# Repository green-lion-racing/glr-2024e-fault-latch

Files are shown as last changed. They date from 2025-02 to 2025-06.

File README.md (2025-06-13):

# Fault latch for IMD and BMS/AMS

This board is a fork of [JacobParent7/FSAE_ELECTRONICS](https://github.com/JacobParent7/FSAE_ELECTRONICS/tree/main/Fault%20Latch). Thanks!

### Overview

It is stripped down for our purposes of using it just as a fault latch if either IMD or BMS signal an error. So it can open and close the SDC (Shutdown circuit).

As input it needs +12V and GND. It also takes a high input of both IMD and BMS to register a fault.

It has two outputs for LEDs, these go into the cockpit of the car, to signal issues to the driver.

Lastly there is one connection where the SDC is routed through.

### Used parts

> [!WARNING]  
> Part list is not available currently.

| Article | Description | Link | Quantity |
| --- | --- | ---- | --- |
| | | | |
| | | | |
| | | | |
| | | | |
| | | | |

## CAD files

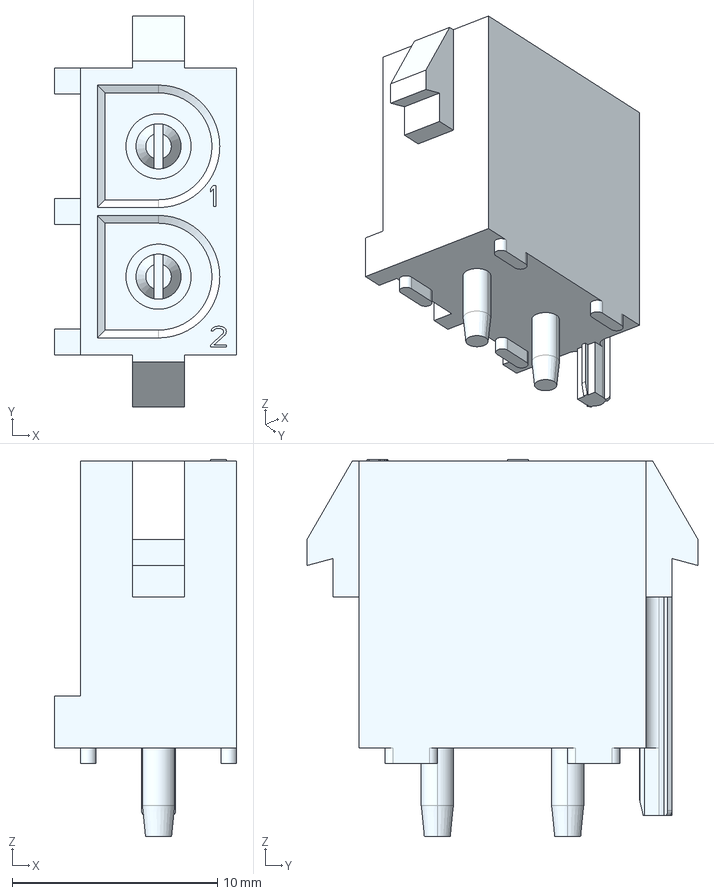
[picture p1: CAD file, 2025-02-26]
DOWNLOADS/CONN/c-641964-1-p-3d.stp
8.89 x 19.1 x 18.4 mm

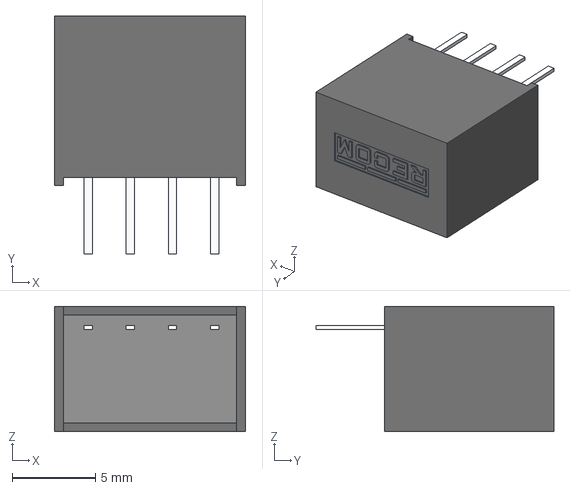
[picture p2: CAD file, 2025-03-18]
DOWNLOADS/ISOLATED_CONVERTER/KiCad/RI-1205S.stp
11.5 x 14.3 x 7.55 mm

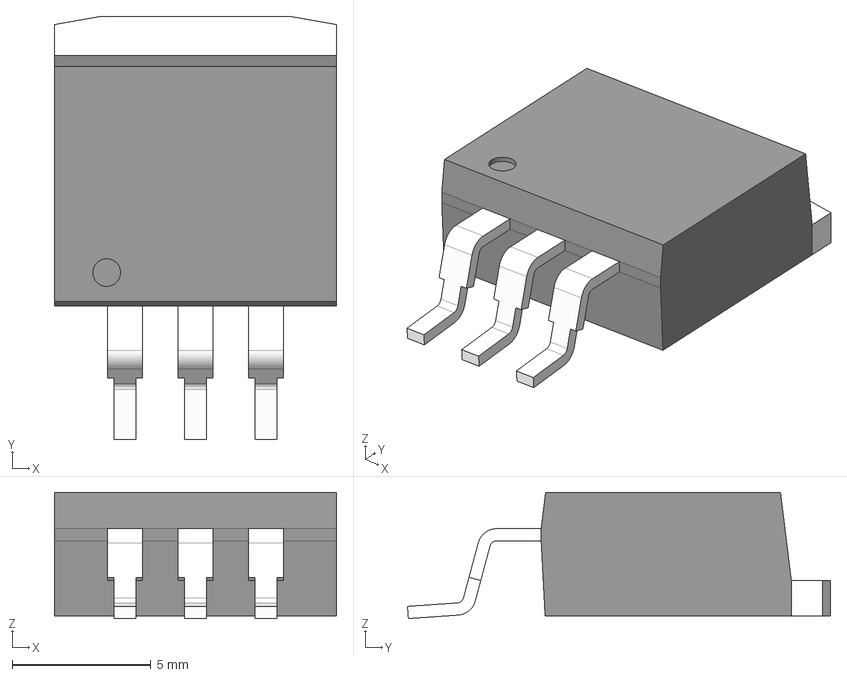
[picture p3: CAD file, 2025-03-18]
DOWNLOADS/REGULATOR/LM7805SX_NOPB.stp
10.2 x 15.2 x 4.54 mm
BODY-TO
HTSINK-TO263
LEAD-TO263 x 3

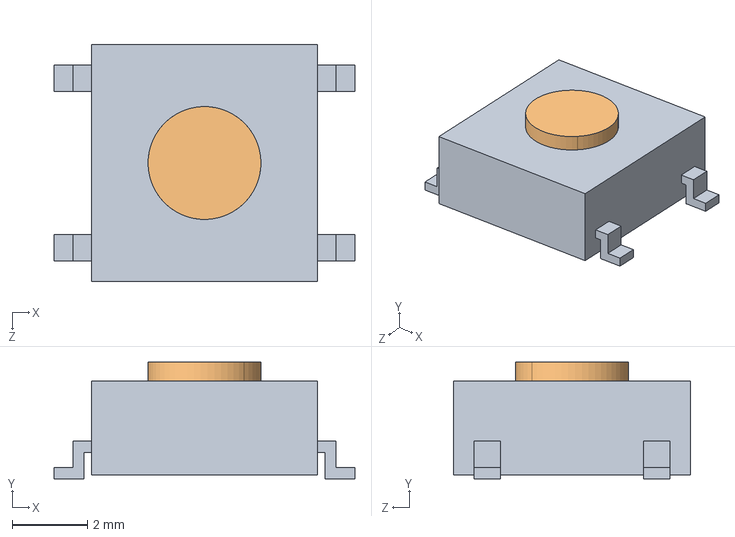
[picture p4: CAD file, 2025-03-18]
DOWNLOADS/SWITCH_3D/B3FS_1000.step
8.00 x 3.10 x 6.30 mm
B3FS_1000_BASE
B3FS_1000_BUTTON

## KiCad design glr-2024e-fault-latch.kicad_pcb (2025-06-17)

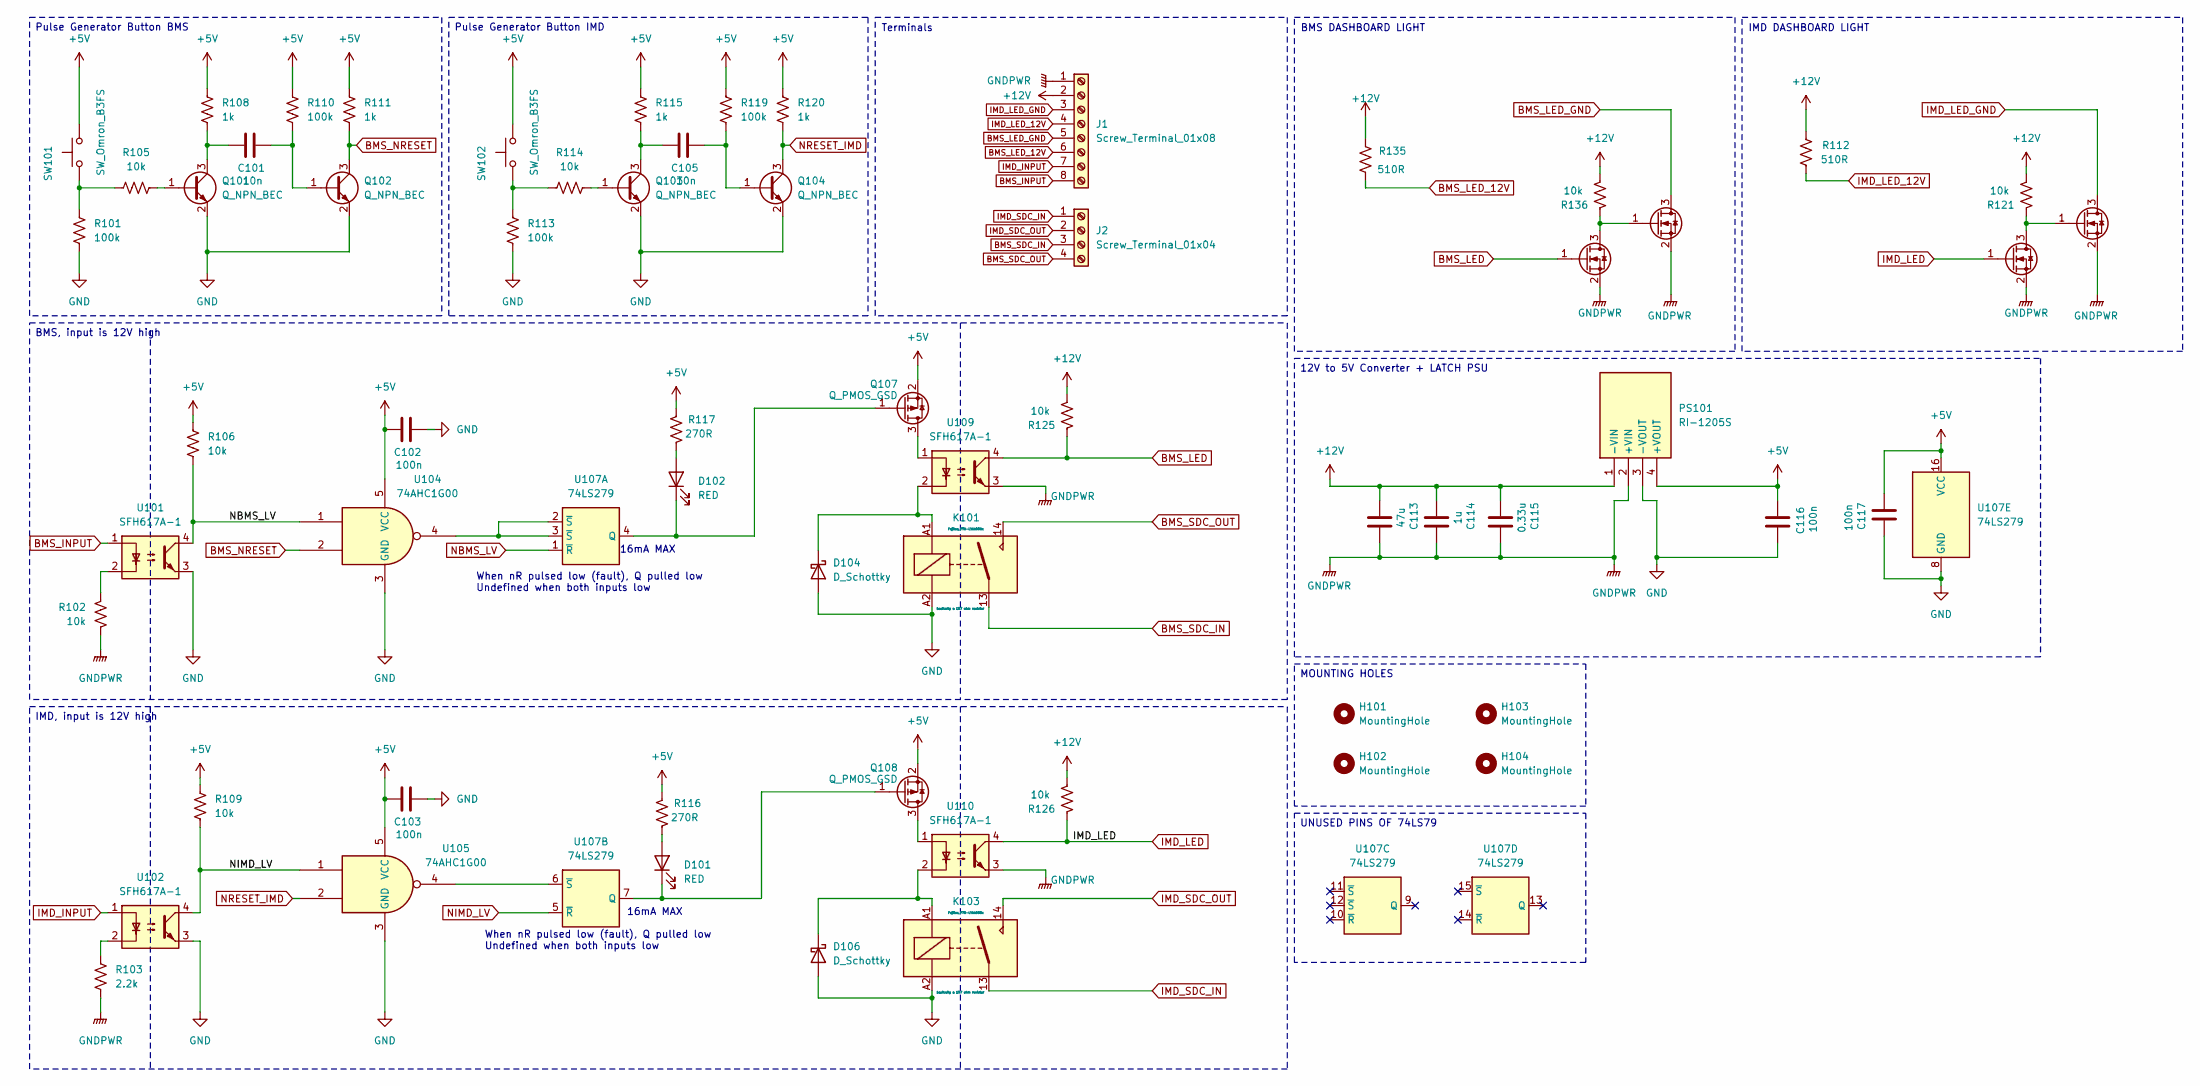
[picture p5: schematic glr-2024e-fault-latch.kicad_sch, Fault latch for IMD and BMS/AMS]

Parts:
C101, C105: 10n; C_0603_1608Metric_Pad1.08x0.95mm_HandSolder; JLC# C1589
C102, C103, C116, C117: 100n; C_0603_1608Metric_Pad1.08x0.95mm_HandSolder; JLC# C1591
C113: 47u; CP_Elec_6.3x5.4; JLC# C2836440
C114: 1u; C_0805_2012Metric_Pad1.18x1.45mm_HandSolder; JLC# C91186
C115: 0.33u; C_0603_1608Metric_Pad1.08x0.95mm_HandSolder; JLC# C282682
D101, D102: RED; LED_0805_2012Metric_Pad1.15x1.40mm_HandSolder; JLC# C19171391
D104, D106: D_Schottky; D_SMA; JLC# C8678
H101, H102, H103, H104: MountingHole; MountingHole_3.2mm_M3
J1: Screw_Terminal_01x08; WECO-950-FB-08
J2: Screw_Terminal_01x04; WECO-950-FB-04
K101, K103: Fujitsu_FTR-LYAA005x; Relay_SPST-NO_Fujitsu_FTR-LYAA005x_FormA_Vertical; MOUSER 817-FTR-LYAA005Y
PS101: RI-1205S; RI0505S; Mouser Part Number 919-RI-1205S
Q101, Q102, Q103, Q104: Q_NPN_BEC; SOT-23; JLC# C2146
Q105, Q106, Q114, Q115: Q_NMOS_GSD; SOT-23; JLC# C151421
Q107, Q108: Q_PMOS_GSD; SOT-523; JLC# C96676
R101, R110, R113, R119: 100k; R_0805_2012Metric_Pad1.20x1.40mm_HandSolder; JLC# C149504
R102, R106, R109, R121, R125, R126, R136: 10k; R_0805_2012Metric_Pad1.20x1.40mm_HandSolder; MOUSER ESR10EZPD1002
R103: 2.2k; R_0805_2012Metric_Pad1.20x1.40mm_HandSolder; JLC# C17520
R105, R114: 10k; R_0805_2012Metric_Pad1.20x1.40mm_HandSolder; JLC# C17414
R108, R111, R115, R120: 1k; R_0805_2012Metric_Pad1.20x1.40mm_HandSolder; JLC# C17513
R112, R135: 510R; R_0603_1608Metric; MOUSER KTR03EZPF5100
R116, R117: 270R; R_0805_2012Metric_Pad1.20x1.40mm_HandSolder; JLC# C17590
SW101, SW102: SW_Omron_B3FS; SW_SPST_Omron_B3FS-100xP; JLC# C271750
U101, U102, U109, U110: SFH617A-1; DIP-4_W7.62mm; MOUSER SFH617A-1X007T
U104, U105: 74AHC1G00; SOT-23-5; JLC# C350556
U107: 74LS279; SOIC-16_3.9x9.9mm_P1.27mm; MOUSER 595-SN74LS279ADR

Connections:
+5V: C102.1, C103.1, C116.2, C117.1, PS101.4 (+VOUT), Q107.2 (S), Q108.2 (S), R106.1, R108.1, R109.1, R110.1, R111.1, R115.1, R116.2, R117.2, R119.1, R120.1, SW101.2, SW102.2, U104.5 (VCC), U105.5 (VCC), U107.16 (VCC)
+12V: C113.2, C114.2, C115.2, J1.2, PS101.1 (-VIN), R112.1, R121.1, R125.1, R126.1, R135.1, R136.1
BMS_INPUT: J1.8, U101.1
BMS_LED: Q114.1 (G), R125.2, U109.4
BMS_LED_12V: J1.6, R135.2
BMS_LED_GND: J1.5, Q115.3 (D)
BMS_NRESET: Q102.3 (C), R111.2, U104.2
BMS_SDC_IN: J2.3, K101.13
BMS_SDC_OUT: J2.4, K101.14
GND: C102.2, C103.2, C116.1, C117.2, D104.2 (A), D106.2 (A), K101.A2, K103.A2, PS101.3 (-VOUT), Q101.2 (E), Q102.2 (E), Q103.2 (E), Q104.2 (E), R101.2, R113.2, U101.3, U102.3, U104.3 (GND), U105.3 (GND), U107.8 (GND)
GNDPWR: C113.1, C114.1, C115.1, J1.1, PS101.2 (+VIN), Q105.2 (S), Q106.2 (S), Q114.2 (S), Q115.2 (S), R102.1, R103.2, U109.3, U110.3
IMD_INPUT: J1.7, U102.1
IMD_LED: Q105.1 (G), R126.2, U110.4
IMD_LED_12V: J1.4, R112.2
IMD_LED_GND: J1.3, Q106.3 (D)
IMD_SDC_IN: J2.1, K103.13
IMD_SDC_OUT: J2.2, K103.14
NBMS_LV: R106.2, U101.4, U104.1, U107.1 (~R)
NIMD_LV: R109.2, U102.4, U105.1, U107.5 (~R)
NRESET_IMD: Q104.3 (C), R120.2, U105.2
unnamed: D101.2 (A), R116.1
unnamed: D101.1 (K), Q108.1 (G), U107.7 (Q)
unnamed: D102.2 (A), R117.1
unnamed: D102.1 (K), Q107.1 (G), U107.4 (Q)
unnamed: D104.1 (K), K101.A1, U109.2
unnamed: D106.1 (K), K103.A1, U110.2
unnamed: Q101.1 (B), R105.1
unnamed: C101.1, Q101.3 (C), R108.2
unnamed: C101.2, Q102.1 (B), R110.2
unnamed: Q103.1 (B), R114.1
unnamed: C105.1, Q103.3 (C), R115.2
unnamed: C105.2, Q104.1 (B), R119.2
unnamed: Q105.3 (D), Q106.1 (G), R121.2
unnamed: Q107.3 (D), U109.1
unnamed: Q108.3 (D), U110.1
unnamed: Q114.3 (D), Q115.1 (G), R136.2
unnamed: R101.1, R105.2, SW101.1
unnamed: R102.2, U101.2
unnamed: R103.1, U102.2
unnamed: R113.1, R114.2, SW102.1
unnamed: U104.4, U107.2 (~S), U107.3 (~S)
unnamed: U105.4, U107.6 (~S)

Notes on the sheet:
16mA MAX
When nR pulsed low (fault), Q pulled low Undefined when both inputs low
BMS, input is 12V high
Pulse Generator Button BMS
Terminals
UNUSED PINS OF 74LS79
Pulse Generator Button IMD
12V to 5V Converter + LATCH PSU
MOUNTING HOLES
BMS DASHBOARD LIGHT
IMD, input is 12V high
IMD DASHBOARD LIGHT

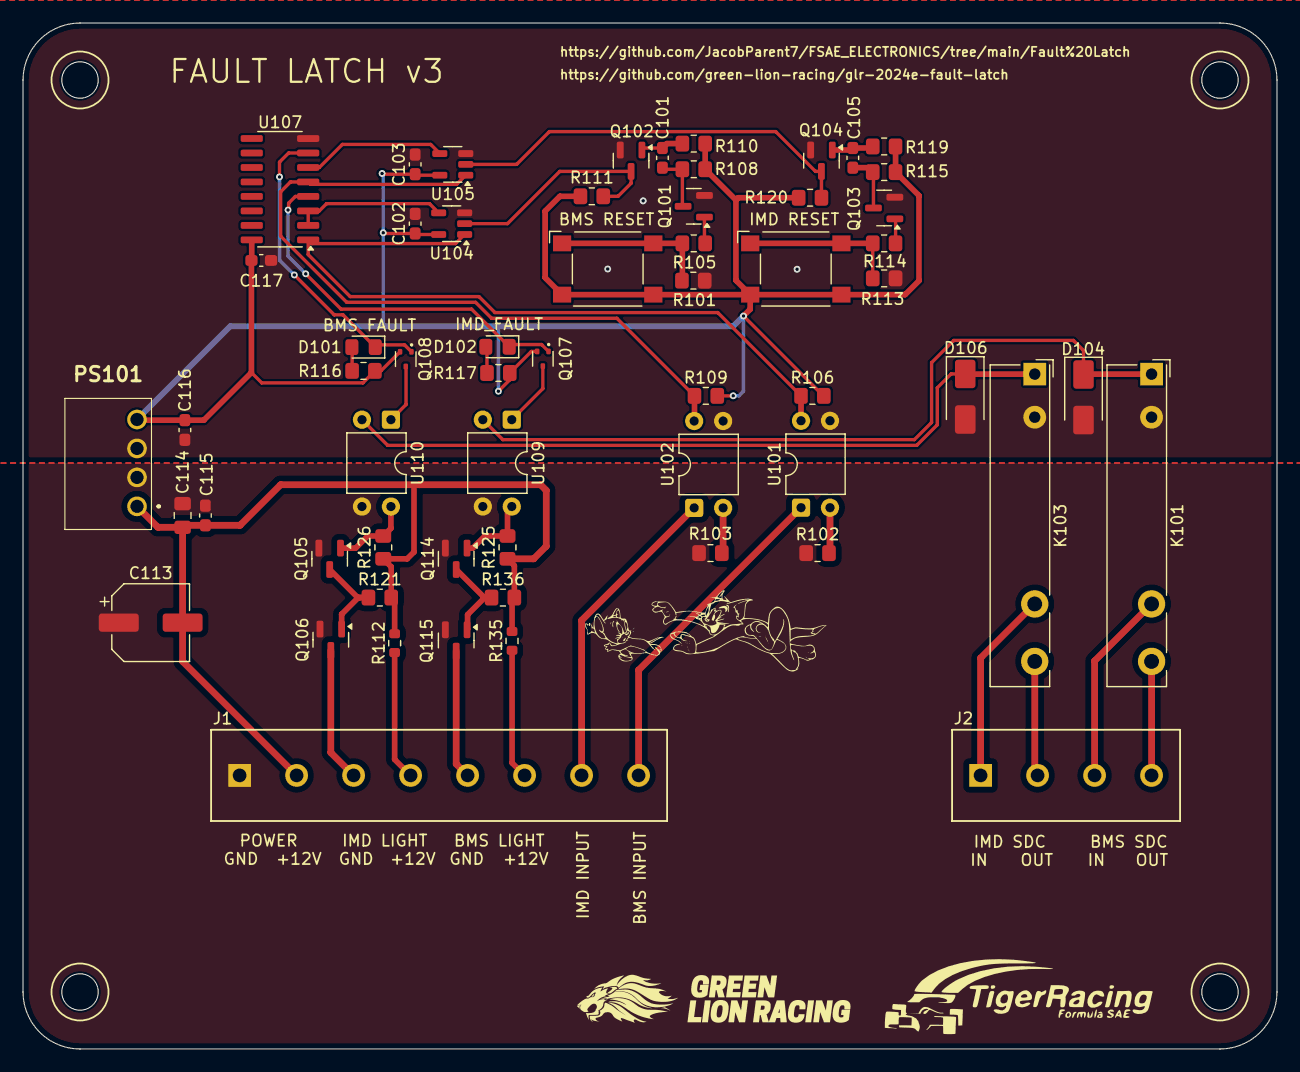
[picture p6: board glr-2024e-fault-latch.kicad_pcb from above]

Board: 2 copper layers, 110.0 x 90.0 mm, 63 parts (0 on the bottom side), 42 nets.

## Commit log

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2025-02-13 Fixed one logical error. Added LT Spice simulation. Pullup Caps, resistor values, schematic layout and cleanup needed.
    [BSPD.kicad_sch]
2025-02-15 Added Current work on Fault Latch
    [Fault Latch 2.kicad_pcb, Fault Latch 2.kicad_sch, Revised Fault Latch Schematic.kicad_pcb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]
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2025-02-19 To Dos on Fault Latch and RML AGAIN.
    [Fault Latch 2.kicad_sch, RML.kicad_pcb, RML.kicad_sch]
2025-02-19 TSSI FIXES
    [TTSI.kicad_sch]
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2025-02-19 TSSI BOM and BYPASS
    [TTSI.kicad_pcb, TTSI.kicad_sch]
2025-02-21 Unfinished version of Fault Latch after applying separate circuits
    [Fault Latch 2.kicad_sch]
2025-02-21 Fault Latch Revision without PSpice Check
    [Fault Latch 2.kicad_sch]
2025-02-21 RML Fixes
    [RML.kicad_sch]
2025-02-21 Comments on BSPD, TSSI
    [BSPD.kicad_sch, TTSI.kicad_sch]
2025-02-22 Added theory of operation to BSPD
    [BSPD.kicad_sch]
2025-02-24 Edits to Fault Latch and TSSI
    [Fault Latch 2.kicad_sch, TTSI.kicad_sch]
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2025-03-02 Added series resistor to RML
    [RML.kicad_sch]
2025-03-02 Added footprints,implemented changes from meeting, starting layout
    [BSPD.kicad_pcb, BSPD.kicad_sch, D0014A.stp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]
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2025-03-08 Fixed the logic for IMD and BSPD
    [Fault Latch 2.kicad_sch]
2025-03-09 Added some footprints but also realized stuff about rules we need to change fault latch for
    [Fault Latch 2.kicad_pcb, Fault Latch 2.kicad_sch]
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2025-03-12 TSSI and FL fixes
    [Fault Latch 2.kicad_sch, TTSI.kicad_pcb, TTSI.kicad_sch]
2025-03-12 Added the pulse generators for the buttons
    [Fault Latch 2.kicad_sch]
2025-03-16 Few changes to BOM as well as added 12v to bunny ears
    [TTSI.kicad_pcb, TTSI.kicad_sch]
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2025-03-21 add useful commit messages they say
    [RML.kicad_sch]
2025-03-21 R,C values for 555. Layout start
    [TTSI.kicad_pcb, TTSI.kicad_sch]
2025-03-22 Layout, routing, footprint addition, constraints set. Some component nets might be too small idk. But needs revision
    [R_78E5_0_0_5 (1).stp, TTSI.kicad_pcb, TTSI.kicad_sch]
2025-03-22 Connector changes, layout, edge cuts, constraints. Need advice on output PMOS
    [641964_1.stp, BSPD.kicad_pcb, BSPD.kicad_sch]
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2025-03-26 Redone logic for BSPD.
    [BSPD.kicad_pcb, BSPD.kicad_sch, TTSI.kicad_pcb]
2025-03-28 Tried to do traces of Fault Latch
    [Fault Latch 2.kicad_pcb]
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2025-03-30 NO ERROR FAULT LATCH.
    [Fault Latch 2.kicad_pcb]
2025-03-30 Found jlcpart for dcdc converter. It's chinese
    [Fault Latch 2.kicad_sch]
2025-03-30 Broken pcb
    [RML.kicad_pcb, RML.kicad_sch]
2025-04-01 Not correct footprints...need to change later.
    [RML.kicad_pcb, RML.kicad_sch]
2025-04-03 Changes to RML and TSSI
    [RML.kicad_sch, TTSI.kicad_sch]
2025-04-07 showed an error on the fault latch
    [Fault Latch 2.kicad_sch]
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2025-04-08 Updated Charging PCB Layout
    [Charging_PCB.kicad_pcb, Charging_PCB.kicad_sch]
2025-04-09 unfinished connector addition to schematic
    [Charging_PCB.kicad_pcb, Charging_PCB.kicad_sch]
2025-04-10 added connectors, relay traces, mounting holes, labels
    [B3FS_1000.step, Charging_PCB.kicad_pcb, Charging_PCB.kicad_sch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]
2025-04-11 cleaned up fault latch a little
    [Fault Latch 2.kicad_pcb, Fault Latch 2.kicad_sch]
2025-04-11 Fillet edges, shrunk relay traces, fixed labels for vinh
    [Charging_PCB.kicad_pcb]
2025-04-12 Finished all part#'s. generated gerber and BOM files
    [Charging_BOM.csv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]
2025-04-15 minor updates to fault latch and RML pcb layout
    [Fault Latch 2-B_Cu.gbl, Fault Latch 2-B_Mask.gbs, Fault Latch 2-B_Paste.gbp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]
2025-04-15 Compacted PCB, and finished BOM,CPL,Gerbers(Charging)
    [Charging_BOM.csv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]
2025-04-15 Added changes to RML and re-routed to fit on 1 layer
    [RML.kicad_pcb, RML.kicad_sch]
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2025-04-15 JLC PCB BOM, placement redone to account for footprint changes, started re-routing
    [BSPD.kicad_pcb, BSPD.kicad_sch]
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2025-04-15 Fixed some errors on TSSI
    [TTSI.kicad_pcb]
2025-04-15 Fixed RML footprint issues
    [RML.kicad_pcb, RML.kicad_sch]
2025-04-15 Fixed TSSI footprint issues
    [TTSI.kicad_pcb, TTSI.kicad_sch]
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2025-04-16 BSPD Fixes
    [BSPD.kicad_pcb, BSPD.kicad_sch]
2025-04-16 Fixed bad PMOS footprint and symbol, fixed gerbers/BOM/CPL
    [Charging_BOM.csv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]
2025-04-16 resolved DRC errors for via sizes and footprints.
    via size changed to 6mm/3mm should still work for JLC. Connected unconnected items. Changed footprints to fix overlap issue
    [BSPD.kicad_pcb]
2025-04-17 TSSI has been integrated into fault latch.
    [BSPD.kicad_pcb, Fault Latch 2.kicad_pcb, Fault Latch 2.kicad_sch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]
2025-04-17 Almost complete merge of fault latch and tssi, footprint still not working for PMOS
    [Fault Latch 2.kicad_sch]
2025-04-18 FIXED PMOS
    [Fault Latch 2.kicad_pcb, Fault Latch 2.kicad_sch]
2025-04-18 Fault Latch V2.0 Prototype
    [Fault Latch 2.kicad_pcb]
2025-04-18 Fault Latch V2.0 waiting for final check
    [Fault Latch 2.kicad_pcb, Fault Latch 2.kicad_sch, RML.kicad_pcb]
2025-04-19 BSPD needs to be fixed + Fault Latch Layout Issue
    [BSPD.kicad_pcb, BSPD.kicad_sch, Fault Latch 2.kicad_pcb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]
2025-04-19 Fault latch added Logo
    [BSPD.kicad_pcb, Charging_PCB.kicad_pcb, Fault Latch 2.kicad_pcb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]
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2025-04-19 Fixed Fault Latch Layout
    [Fault Latch 2.kicad_pcb]
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2025-04-19 Finished schematic with added SR latch and new buttons, started layout
    [Charging_PCB-B_Cu.gbl, Charging_PCB-B_Mask.gbs, Charging_PCB-B_Paste.gbp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]
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2025-04-19 Double checked PMOS output logic. Added connector and routing for sense wires from sensors. Connected one unconnected track. 2 DRC errors about spokes, but otherwise Ready to Geaux :3
    [BSPD.kicad_pcb, BSPD.kicad_sch]
2025-04-21 Added SR Latch to charging PCB, completed gerbers,bom,and CPL file and added mouser parts list to assembly file
    [Charging_PCB.kicad_pcb, Charging_PCB.kicad_sch, bom.csv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]
2025-04-21 Fault Latch Updated and generated gerber files
    [BSPD.kicad_pcb, BSPD.kicad_sch, Fault Latch 2.csv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]
2025-04-22 Added charging wiring schematic with wire gauges for connection to accumulator
    [Accumulator_Charging_Schematic.kicad_sch]
2025-04-22 Fixed gerbers for RML and FaultLatch
    [Fault Latch 2-B_Cu.gbl, Fault Latch 2-B_Mask.gbs, Fault Latch 2-B_Paste.gbp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]
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2025-04-23 BSPD now active low output, fault latch rerouted.
    [BSPD.kicad_pcb, Fault Latch 2.kicad_pcb, Fault Latch 2.kicad_sch]
2025-04-23 Manufacturing generated for BSPD and Fault Latch
    [BSPD-B_Cu.gbr, BSPD-B_Mask.gbr, BSPD-B_Paste.gbr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]
2025-04-23 Double checked schematic. Fixed wrong connection on comparators and did re-routed the signals. Added new simulation with 555 timer and double cchecked that it is active low performing
    [BSPD.kicad_pcb, BSPD.kicad_sch]
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2025-06-03 ESF documentation and wiring schematics for charging
    [Accumulator_Charging_Schematic.kicad_sch, Cart_Wiring_Schematic.kicad_pcb, Cart_Wiring_Schematic.kicad_sch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]
2025-06-11 initial fork
    remove everything except fault latch stuff
    [Accumulator_Charging_Schematic.kicad_sch, B3FS_1000.step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]
2025-06-12 work in progress
    keep only bms and imd
    remove tssi stuff
    [glr-2024e-fault-latch.kicad_pcb, glr-2024e-fault-latch.kicad_sch]
2025-06-13 almost finished
    add bms light logic
    improve overall placements of components
    improve routing
    improve silk component identifiers
    [glr-2024e-fault-latch.kicad_pcb, glr-2024e-fault-latch.kicad_sch]
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2025-06-17 use to screw terminals
    improve labels in schematic
    [glr-2024e-fault-latch.kicad_pcb, glr-2024e-fault-latch.kicad_sch]
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
